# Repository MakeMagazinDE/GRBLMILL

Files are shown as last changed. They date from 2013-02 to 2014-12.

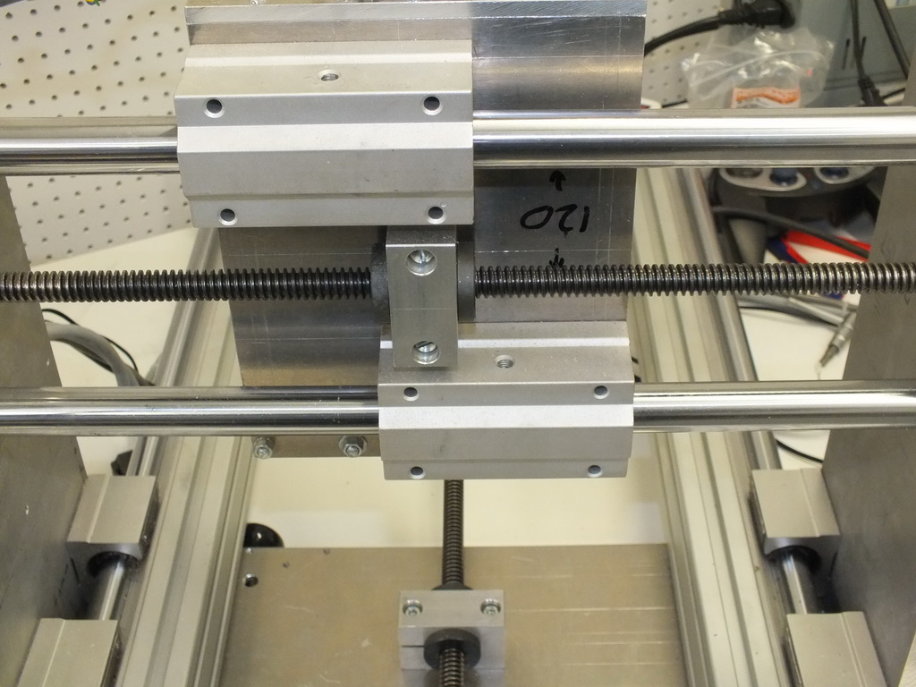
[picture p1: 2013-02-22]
BILDER/DSCF5111.JPG

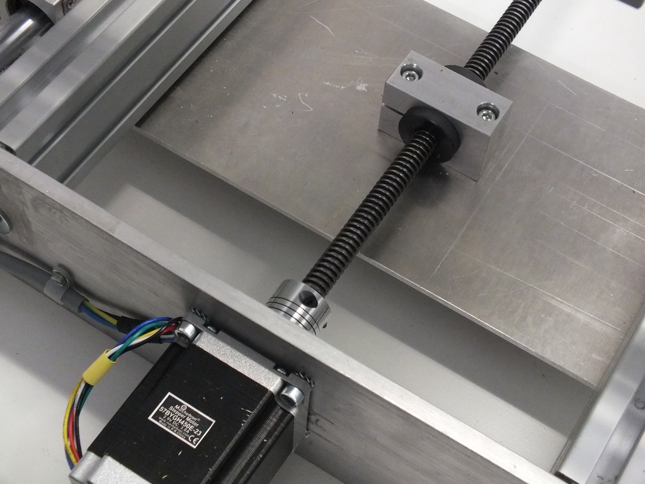
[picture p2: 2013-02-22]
BILDER/DSCF5087.JPG

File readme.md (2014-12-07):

GRBLMILL
========

3D-Positionierer/Fräse aus c't Hacks 01/2013

Verzeichnis GRBL: Firmware für Atmel ATmega328 mit Arduino-Bootloader, z.B. AT-Mini Board von mikroElektronika

- Mechanische Pläne für Selbstbau-Fräse
- Bezugsquellen
- Original-Unterlagen chin. Hersteller

Alle Angaben ohne Gewähr

Schaltbilder zu chinesischen TB6560-Schrittmotortreiberkarten 
und unsere GRBL-Schrittmotorsteuerung siehe auch Repo heise/TB6560-BOARDS

Obsoletes Projekt. Für neuere Aufbauten empfehlen wir unser Pojekt GRBL-Jogger (siehe Repository GRBL-JOG).

by Carsten Meyer, c't Hacks (cm@ct.de)

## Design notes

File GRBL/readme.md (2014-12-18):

Note: Obsolete project. Please use heise/GRBL-JOG instead.

h1. Grbl - An embedded g-code interpreter and motion-controller for the Arduino/AVR328 microcontroller
    
Grbl is a no-compromise, high performance, low cost alternative to parallel-port-based motion control for CNC milling. It will run on a vanilla Arduino (Duemillanove/Uno) as long as it sports an Atmega 328. 

The controller is written in highly optimized C utilizing every clever feature of the AVR-chips to achieve precise timing and asynchronous operation. It is able to maintain more than 30kHz of stable, jitter free control pulses.

It accepts standards-compliant G-code and has been tested with the output of several CAM tools with no problems. Arcs, circles and helical motion are fully supported, as well as, other basic functional g-code commands. Functions and variables are not currently supported, but may be included in future releases in a form of a pre-processor.

Grbl includes full acceleration management with look ahead. That means the controller will look up to 18 motions into the future and plan its velocities ahead to deliver smooth acceleration and jerk-free cornering.

*Changelog for v0.8a3 from v0.8 by cm@ct.de:*
  - Q&D Homing implemented on G28 or G30 command
  - M100 command for resetting external pulse counter
  - Defaults for c't Mill project on 3mm or 6mm threads
  - Spindle direction output deleted
  - Supports red "BUSY" LED on MINI-AT board from MikroE.com
  
*Changelog for v0.8 from v0.7:*
  - *ALPHA status: _Under heavy development. Code state may significantly change with each push as new features are integrated._*
  - Major structural overhaul to allow for multi-tasking events and new feature sets
  - New run-time command control: Feed hold (pause), Cycle start (resume), Reset (abort), Status reporting
  - Controlled feed hold with deceleration to ensure no skipped steps and loss of location.
  - After feed hold, cycle accelerations are re-planned and may be resumed.
  - Re-factored g-code parser with robust error-checking.
  - Work coordinate system (G54), offsets(G92), and machine coordinate system support. G10 work coordinate settings support. (Up to 6 work coordinate systems(G54-G59) available as a compile-time option.)
  - Program stop(M0,M1*,M2,M30) initial support. Optional stop to do.
  - System reset re-initializes grbl without resetting the Arduino and retains machine/home position and work coordinates.
  - Restructured planner and stepper modules to become independent and ready for future features.
  - Planned features: Jog mode, status reporting, runtime settings such as toggling block delete, XON/XOFF flow control.
  - Reduce serial read buffer to 128 characters and increased write buffer to 64 characters.
  - Misc bug fixes and removed deprecated acceleration enabled code.

*Important note for Atmega 168 users:* Going forward, support for Atmega 168 will be dropped due to its limited memory and speed. However, legacy Grbl v0.51 "in the branch called 'v0_51' is still available for use.

_The project was initially inspired by the Arduino GCode Interpreter by Mike Ellery_

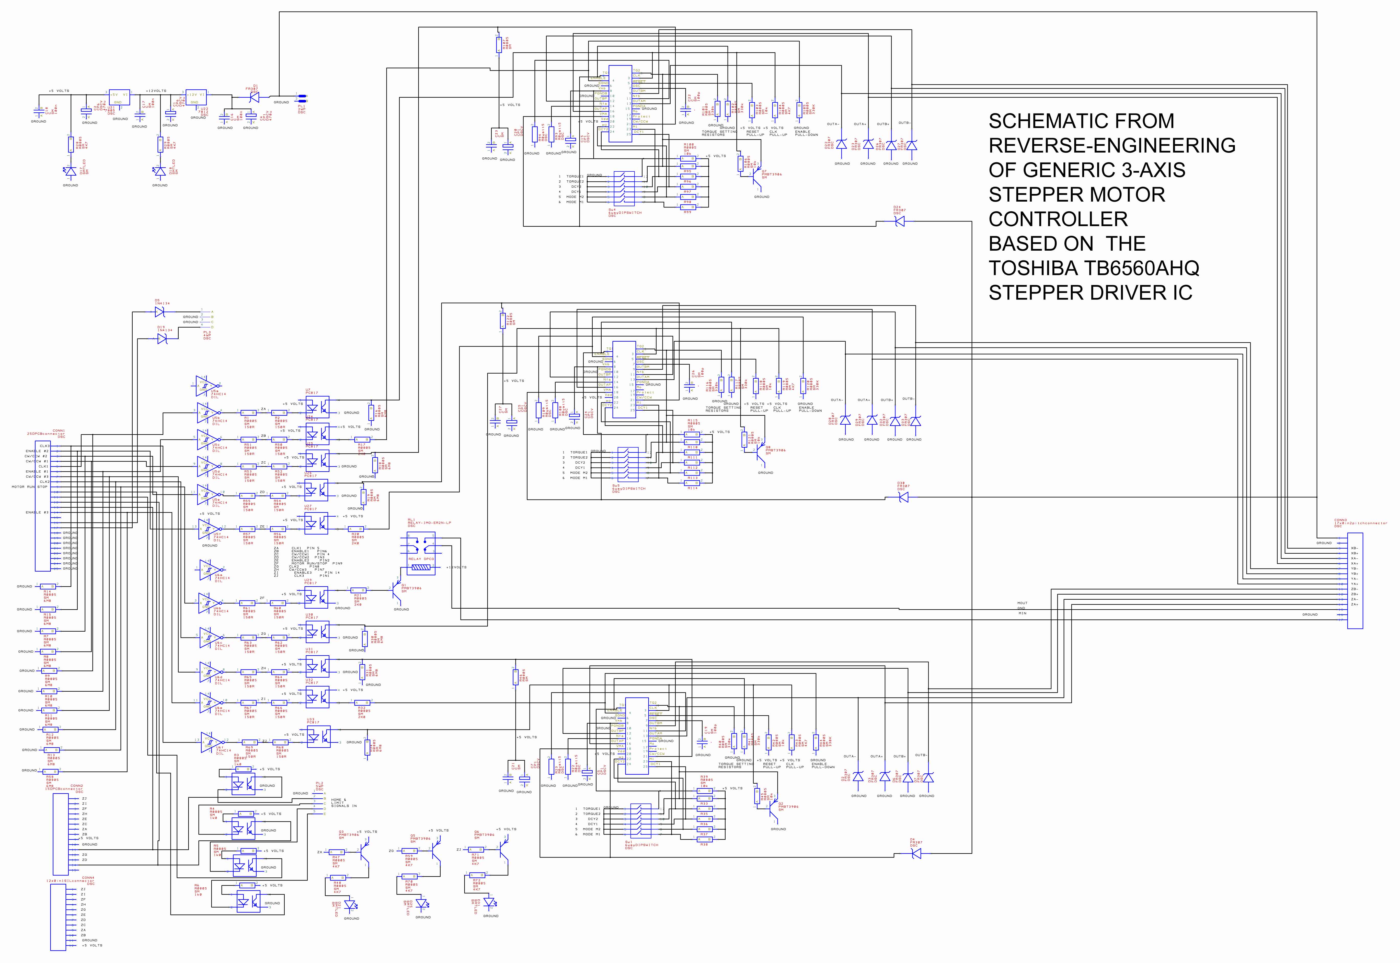
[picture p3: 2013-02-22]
GRBL/doc/REVERSESTEPPER.jpg

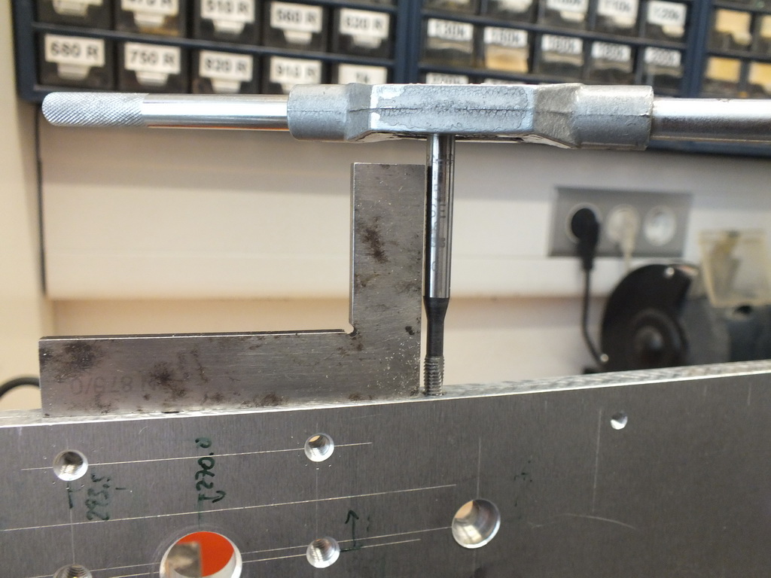
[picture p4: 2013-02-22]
BILDER/bild5.JPG

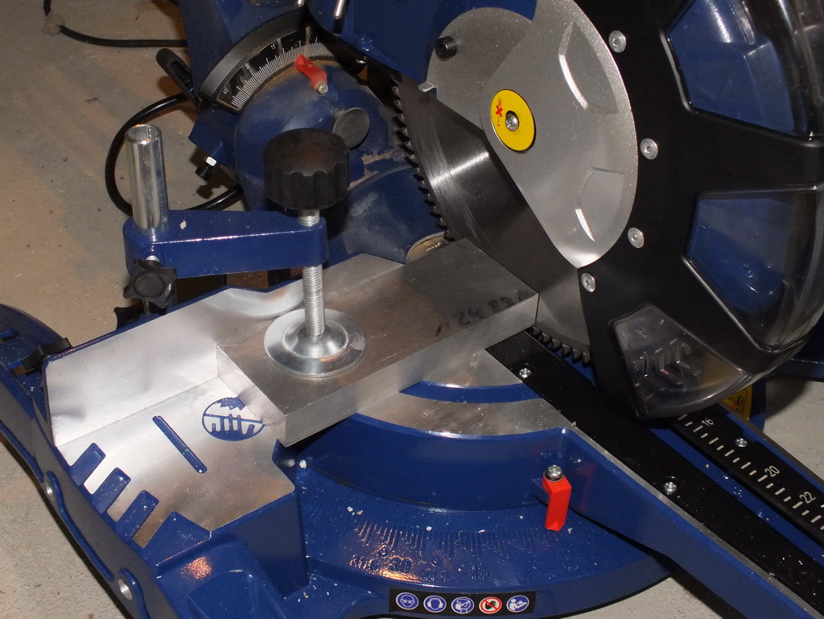
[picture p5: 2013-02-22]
BILDER/bild7.JPG

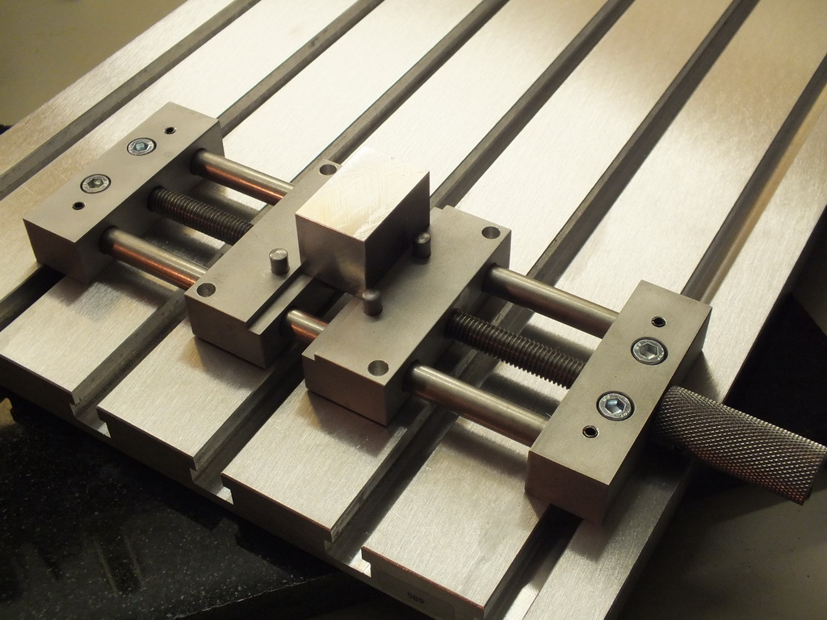
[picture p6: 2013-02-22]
BILDER/bild22.JPG

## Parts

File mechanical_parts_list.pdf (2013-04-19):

Stückliste c't-Portalfräse | Version 600 x 300 mm
Pos. | Bezeichnung | Abmessungen/Anmerkung | Stück | Einzelpreis Gesamtpreis Lieferant

X-Achse und Rahmen
1 | CNC Set 20 x 600 supported, "grün", 4 Wagen | 20 x 600 mm | 1 | 75,50 € | 75,50 € | http://stores.ebay.de/cnc-discount
2 | Hammermuttern | M5 Nut 8 | 20 | 0,28 € | 5,60 € | http://stores.ebay.de/aluprofiltechnik
3 | Alu-Profil Nut 8 | 60 x 30 Nut 8, 600 mm | 2 | 8,10 € | 16,20 € | http://stores.ebay.de/aluprofiltechnik
4 | Alu-Platte vorn/hinten | 80 x 420 x 8 mm Alu-Platte 2017 | 2 | 8,00 € | 16,00 € | http://www.metall-kunststoffhandel.de/shop/
| Y-Achse
5 | Y-Portal seitlich | 150 x 350 x 10 mm Alu-Platte 2017 | 2 | 11,87 € | 23,74 € | http://www.metall-kunststoffhandel.de/shop/
6 | Y-Traverse oben, Y-Traverse unten | 150 x 420 x 5 mm Alu-Blech 2017 | 2 | 16,44 € | 32,88 € | http://www.metall-kunststoffhandel.de/shop/
7 | Präzisionswelle | 20 x 400 mm | 2 | 8,80 € | 17,60 € | http://stores.ebay.de/Metallbau-Pietrzak
8 | Linearlager (ET)SCS20LUU | | 2 | 12,95 € | 25,90 € | http://stores.ebay.de/mayerundschulze-maschinen
9 | Linearlager (ET)SCS20UU | Alternative zu Pos. 8: 4x | 0 | 6,95 € | 0,00 € | http://stores.ebay.de/mayerundschulze-maschinen
10 | Wellenhalter Wandmontage (ET)SHF20 | falls Welle ohne Gewinde | 4 | 4,90 € | 19,60 € | http://stores.ebay.de/mayerundschulze-maschinen
| Z-Achse
11 | Präzisionswelle | 16 x 200 mm | 2 | 4,00 € | 8,00 € | http://stores.ebay.de/Metallbau-Pietrzak
12 | Linearlager (ET)SCS16LUU | | 2 | 11,25 € | 22,50 € | http://stores.ebay.de/mayerundschulze-maschinen
13 | Wellenhalter (ET)SK16 stehend | | 2 | 3,50 € | 7,00 € | http://stores.ebay.de/mayerundschulze-maschinen
14 | CNC Linearführung 16x 200mm Set "Blau" | Alternative zu Pos. 11 bis 13: 1x | 0 | 51,60 € | 0,00 € | http://stores.ebay.de/cnc-discount
15 | Wellenhalter Wandmontage (ET)SHF16 | | 2 | 3,50 € | 7,00 € | http://stores.ebay.de/mayerundschulze-maschinen
16 | Z-Träger Grundplatte | 200 x 155 x 8 mm Alu-Platte 2017 | 1 | 7,02 € | 7,02 € | http://www.metall-kunststoffhandel.de/shop/
17 | Spindelmotor-Träger | 130 x 155 x 8 mm Alu-Platte 2017 | 1 | 6,62 € | 6,62 € | http://www.metall-kunststoffhandel.de/shop/
18 | Schrittmotorträger oben | 65 x 155 x 6 mm Alu-Platte 2017 | 1 | 5,10 € | 5,10 € | http://www.metall-kunststoffhandel.de/shop/
| Sonstiges
19 | Nylatron-Muttern | TR12x3 mit Rändel, halb | 6 | 3,95 € | 23,70 € | http://www.cnc-laden.de
20 | Mutterblock zum Klemmen | 54 x 35 x 24 mm, TR12 | 3 | 14,60 € | 43,80 € | http://www.cnc-laden.de
21 | Trapezspindel | TR12x3, 1000 mm | 2 | 6,70 € | 13,40 € | http://stores.ebay.de/Metallbau-Pietrzak
22 | Wellenkupplung 6,35/12 flexibel | China: ca. 4 € | 2 | 8,00 € | 16,00 € | http://stores.ebay.de/dold-mechatronik
23 | Wellenkupplung 6,35/12 starr | für Z-Achse, ggf. aufbohren auf 12 mm 1 | 6,00 € | 6,00 € | http://stores.ebay.de/dold-mechatronik
24 | Flanschlager Mini 12 mm, KFL001 | | 4 | 6,78 € | 27,12 € | http://www.kugellager-express.de
25 | Spannhals-Befestigung 43mm | Aufnahme etwas zu groß (44mm)! | 1 | 24,30 € | 24,30 € | http://www.cnc-laden.de
26 | Hammermuttern | M6 Nut 8 | 10 | 0,28 € | 2,80 € | http://stores.ebay.de/aluprofiltechnik
| Gesamt | | | | 453,38 €
Z-Achse Alternative | schmaler, auch zum Betrieb mit Gravuranschlag, 50 mm Verfahrweg
Linearlager mit quadratischem Flansch 16mm LMEK16UU | 2 | 7,20 € | http://stores.ebay.de/dold-mechatronik
| Linearlager 16mm SCE16SUU | | 4 | 7,90 € | | http://stores.ebay.de/dold-mechatronik
| CNC Linearführung 16x 250mm Set "Blau" | | 1 | 54,00 € | 54,00 € | http://stores.ebay.de/cnc-discount
| Z-Träger Grundplatte | 200 x 135 x 8 mm Alu-Platte 2017 | 1 | 7,02 € | 7,02 € | http://www.metall-kunststoffhandel.de/shop/
| Spindelmotor-Träger | 130 x 135 x 8 mm Alu-Platte 2017 | 1 | 6,62 € | 6,62 € | http://www.metall-kunststoffhandel.de/shop/
| Schrittmotorträger oben | 65 x 135 x 6 mm Alu-Platte 2017 | 1 | 5,10 € | 5,10 € | http://www.metall-kunststoffhandel.de/shop/
| Zubehör
27 | Spannhals-Adapter 43 mm auf Ferm oder Drehmel | | 0 | 23,00 € | 0,00 € | http://www.cnc-laden.de
28 | Fräsmotor Kress FME-1051 | | 0 | 173,00 € | 0,00 € | http://www.amazon.de
29 | Fräsmotor Noname | Alternative zu Pos. 28 | 1 | 54,00 € | 54,00 € | http://myworld.ebay.de/jancocaucau3/
30 | T-Nutenplatte 4030 | 400 x 300 mm | 0 | 129,00 € | 0,00 € | http://www.maschinen-werkzeuge.com
31 | Vakuumtische | diverse | 0 | | 0,00 € | http://www.vakuumtisch.de/
32 | Spannpratzen-Satz M6 | | 0 | 64,00 € | 0,00 € | http://stores.ebay.de/CNC-Maschinen-Shop
33 | Schrittmotor NEMA23 1 Nm, 2 A | 57x 57 mm Flansch | 0 | 29,90 € | 0,00 € | http://www.frasa-cnc.de
34 | Schrittmotor NEMA23 1,85 Nm, 2 A | Alternative zu Pos. 32 | 0 | 37,90 € | 0,00 € | http://stores.ebay.de/CNCShop-at
35 | Schrittmotorsteuerung TB6560 | | 0 | 29,90 € | 0,00 € | diverse ebay-Anbieter
36 | Schrittmotorsteuerung TB6560 | Alternative zu Pos. 34 | 0 | 32,89 € | 0,00 € | http://stores.ebay.de/1-netshop-best
37 | Not-Aus-Schalter Aufputz | | 1 | 12,95 € | 12,95 € | http://stores.ebay.de/klinger-und-born
| Alternativprodukte (ggf. Änderung nötig)
| Trapezspindeln TR12 x 6 mit Muttern | Alternative zu TR12x3, 1000 mm | 2 | | | http://stores.ebay.de/dold-mechatronik
| (doppelte Steigung wie TR12x3, schnellerer Eilgang)
| Flanschlager für X-Achse, UCF201 (größer) | | 1 | 4,40 € | 4,40 € | http://stores.ebay.de/Panta-Shop
| Kugelumlauf-Führungen, Kugelumlauf-Spindeln | diverse | | | | http://stores.ebay.de/Linear-Motion-Products

## Technische Daten

| Verfahrweg | 450 x 245 mm | | | | Alle Angaben ohne Gewähr.
| Durchlasshöhe | 85 mm | | | | Stand 19.04.2013
| Verfahrgeschwindigkeit, Eilgang | 1500 mm/min (2800 bei 6mm Trapezsp.) | | | | Statt Alu 2017 auch Qualität 2007 verwendbar.
| Stromversorgung | 24V/5A | | | | Autor: Carsten Meyer, Redaktion c't Hacks, cm@ct.d

Artikel-Link

http://www.ebay.de/itm/CNC-Set-20-x-600mm-Linearfuhrung-Linear-Guide-Rail-Stage-Frase-Welle-/221043413143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

http://www.ebay.de/itm/Profil-30-x-60-Nut-8-Aluprofil-Profil-Aluminium-Alu-/150655377758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

http://www.metall-kunststoffhandel.de/shop/2007-flachstange-p-147.html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

http://www.ebay.de/itm/Prazisionswelle-16-mm-100-990mm-wahlbar-20-m-Tol-h6-geschliffen-cf53-1511-/390416782056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

http://cnc-laden.de/cnc-shop/Trapezgewindemuttern-12x3/Trapezgewindemutter-12x3-Nylatron-Raendel.htmlhttp://cnc-laden.de/cnc-shop/Mutterbloecke/Mutterblock-Trapezgew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

http://www.kugellager-express.de/Gehaeuselager/Miniatur-Flanschlager-KFL---/Miniatur-Flanschlager-KFL001---Welle--12-mm--SILBER-Serie-.htmlhttp://cnc-laden.de/cnc-sh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

http://www.ebay.de/itm/CNC-Linearfuhrung-16x-200mm-Set-Blau-2x-lange-Linearwagen-Wellen-Wellenhalter-/221171302185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

http://cnc-laden.de/cnc-shop/Spannhals-Adapter.html
http://www.amazon.de/Kress-1050-FME-Watt-Fr%C3%A4smotor/dp/B004U5F4H0

http://www.maschinen-werkzeuge.com/tnutenplatte-4030-p-1372.html

http://www.ebay.de/itm/58-Teiliger-Spannpratzen-Satz-M6-8er-Nut-/260923137767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

e

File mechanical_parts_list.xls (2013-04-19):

Stückliste c't-Portalfräse |  | Version 600 x 300 mm
Pos. | Bezeichnung | Abmessungen/Anmerkung | Stück | Einzelpreis | Gesamtpreis | Lieferant | Artikel-Link
 | X-Achse und Rahmen
1 | CNC Set 20 x 600 supported, "grün", 4 Wagen | 20 x 600 mm | 1 | 75.50 € | 75.50 € | http://stores.ebay.de/cnc-discount | http://www.ebay.de/itm/CNC-Set-20-x-600mm-Linearfuhrung-Linear-Guide-Rail-Stage-Frase-Welle-/221043413143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
2 | Hammermuttern | M5 Nut 8 | 20 | 0.28 € | 5.60 € | http://stores.ebay.de/aluprofiltechnik
3 | Alu-Profil Nut 8 | 60 x 30 Nut 8, 600 mm | 2 | 8.10 € | 16.20 € | http://stores.ebay.de/aluprofiltechnik | http://www.ebay.de/itm/Profil-30-x-60-Nut-8-Aluprofil-Profil-Aluminium-Alu-/150655377758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
4 | Alu-Platte vorn/hinten | 80 x 420 x 8 mm Alu-Platte 2017 | 2 | 8.00 € | 16.00 € | http://www.metall-kunststoffhandel.de/shop/
 | Y-Achse
5 | Y-Portal seitlich | 150 x 350 x 10 mm Alu-Platte 2017 | 2 | 11.87 € | 23.74 € | http://www.metall-kunststoffhandel.de/shop/ | http://www.metall-kunststoffhandel.de/shop/2007-flachstange-p-147.html?osCsid=4d8f5ec64735d1192282b06c5dd4326e
6 | Y-Traverse oben, Y-Traverse unten | 150 x 420 x 5 mm Alu-Blech 2017 | 2 | 16.44 € | 32.88 € | http://www.metall-kunststoffhandel.de/shop/ | http://www.metall-kunststoffhandel.de/shop/aluminium-platte-0050-12017-p-2146_150_420.html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
7 | Präzisionswelle | 20 x 400 mm | 2 | 8.80 € | 17.60 € | http://stores.ebay.de/Metallbau-Pietrzak | http://www.ebay.de/itm/Prazisionswelle-20-mm-100-990mm-wahlbar-22-m-Tol-h6-geschliffen-cf53-1513-/390416782226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
8 | Linearlager (ET)SCS20LUU |  | 2 | 12.95 € | 25.90 € | http://stores.ebay.de/mayerundschulze-maschinen | http://www.ebay.de/itm/Linearlager-Linearwagen-Linearschlitten-SCS20LUU-20-mm-Welle-ETSCS20LUU-/150836635461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
9 | Linearlager (ET)SCS20UU | Alternative zu Pos. 8: 4x | 0 | 6.95 € | 0.00 € | http://stores.ebay.de/mayerundschulze-maschinen | http://www.ebay.de/itm/Linearlager-Linearwagen-Linearschlitten-SCS20UU-20-mm-Welle-ETSCS20UU-/150836635489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
10 | Wellenhalter Wandmontage (ET)SHF20 | falls Welle ohne Gewinde | 4 | 4.90 € | 19.60 € | http://stores.ebay.de/mayerundschulze-maschinen | http://www.ebay.de/itm/Wellenhalter-Wandmontage-Stahlwelle-20-mm-ETSHF20-/150908306739?pt=LH_DefaultDomain_77
 | Z-Achse
11 | Präzisionswelle | 16 x 200 mm | 2 | 4.00 € | 8.00 € | http://stores.ebay.de/Metallbau-Pietrzak | http://www.ebay.de/itm/Prazisionswelle-16-mm-100-990mm-wahlbar-20-m-Tol-h6-geschliffen-cf53-1511-/390416782056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
12 | Linearlager (ET)SCS16LUU |  | 2 | 11.25 € | 22.50 € | http://stores.ebay.de/mayerundschulze-maschinen | http://www.ebay.de/itm/Linearlager-Linearwagen-Linearschlitten-SCS16LUU-16-mm-Welle-ETSCS16LUU-/150836085462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
13 | Wellenhalter (ET)SK16 stehend |  | 2 | 3.50 € | 7.00 € | http://stores.ebay.de/mayerundschulze-maschinen | http://www.ebay.de/itm/Wellenhalter-stehend-Bodenmontage-Stahlwelle-16-mm-ETSK16-/150789522903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
14 | CNC Linearführung 16x 200mm Set "Blau" | Alternative zu Pos. 11 bis 13: 1x | 0 | 51.60 € | 0.00 € | http://stores.ebay.de/cnc-discount | http://www.ebay.de/itm/CNC-Linearfuhrung-16x-200mm-Set-Blau-2x-lange-Linearwagen-Wellen-Wellenhalter-/221171302185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
15 | Wellenhalter Wandmontage (ET)SHF16 |  | 2 | 3.50 € | 7.00 € | http://stores.ebay.de/mayerundschulze-maschinen | http://www.ebay.de/itm/Wellenhalter-Wandmontage-Stahlwelle-16-mm-ETSHF16-/150838904770?pt=LH_DefaultDomain_77
16 | Z-Träger Grundplatte | 200 x 155 x 8 mm Alu-Platte 2017 | 1 | 7.02 € | 7.02 € | http://www.metall-kunststoffhandel.de/shop/ | http://www.metall-kunststoffhandel.de/shop/2007-flachstange-p-131_200_0.html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
17 | Spindelmotor-Träger | 130 x 155 x 8 mm Alu-Platte 2017 | 1 | 6.62 € | 6.62 € | http://www.metall-kunststoffhandel.de/shop/ | http://www.metall-kunststoffhandel.de/shop/2007-flachstange-p-131_200_0.html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
18 | Schrittmotorträger oben | 65 x 155 x 6 mm Alu-Platte 2017 | 1 | 5.10 € | 5.10 € | http://www.metall-kunststoffhandel.de/shop/ | http://www.metall-kunststoffhandel.de/shop/2007-flachstange-p-131_200_0.html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
 | Sonstiges
19 | Nylatron-Muttern | TR12x3 mit Rändel, halb | 6 | 3.95 € | 23.70 € | http://www.cnc-laden.de | http://cnc-laden.de/cnc-shop/Trapezgewindemuttern-12x3/Trapezgewindemutter-12x3-Nylatron-Raendel.html
20 | Mutterblock zum Klemmen | 54 x 35 x 24 mm, TR12 | 3 | 14.60 € | 43.80 € | http://www.cnc-laden.de | http://cnc-laden.de/cnc-shop/Mutterbloecke/Mutterblock-Trapezgewindemutter-12x3-Klemmen.html
21 | Trapezspindel | TR12x3, 1000 mm | 2 | 6.70 € | 13.40 € | http://stores.ebay.de/Metallbau-Pietrzak | http://www.ebay.de/itm/Trapezgewindespindel-TR12x3-rechts-DIN103-150mm-3508-/220385890978?pt=Motoren_Getriebe
22 | Wellenkupplung 6,35/12 flexibel | China: ca. 4 € | 2 | 8.00 € | 16.00 € | http://stores.ebay.de/dold-mechatronik | http://www.ebay.de/itm/Wellenkupplung-Kupplung-RB-flexibel-D25L30-6-35-12-00mm-CNC-Schrittmotor-/270934044860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
23 | Wellenkupplung 6,35/12 starr | für Z-Achse, ggf. aufbohren auf 12 mm | 1 | 6.00 € | 6.00 € | http://stores.ebay.de/dold-mechatronik
24 | Flanschlager Mini 12 mm, KFL001 |  | 4 | 6.78 € | 27.12 € | http://www.kugellager-express.de | http://www.kugellager-express.de/Gehaeuselager/Miniatur-Flanschlager-KFL---/Miniatur-Flanschlager-KFL001---Welle--12-mm--SILBER-Serie-.html
25 | Spannhals-Befestigung 43mm | Aufnahme etwas zu groß (44mm)! | 1 | 24.30 € | 24.30 € | http://www.cnc-laden.de | http://cnc-laden.de/cnc-shop/Spannhals/Spannhals-Maschinenhalter-43-mm.html
26 | Hammermuttern | M6 Nut 8 | 10 | 0.28 € | 2.80 € | http://stores.ebay.de/aluprofiltechnik
 | Gesamt |  |  |  | 453.38 €
 | Z-Achse Alternative | schmaler, auch zum Betrieb mit Gravuranschlag, 50 mm Verfahrweg
 | Linearlager mit quadratischem Flansch 16mm LMEK16UU |  | 2 | 7.20 € |  | http://stores.ebay.de/dold-mechatronik
 | Linearlager 16mm SCE16SUU |  | 4 | 7.90 € |  | http://stores.ebay.de/dold-mechatronik
 | CNC Linearführung 16x 250mm Set "Blau" |  | 1 | 54.00 € | 54.00 € | http://stores.ebay.de/cnc-discount | http://www.ebay.de/itm/CNC-Linearfuhrung-16x-200mm-Set-Blau-2x-lange-Linearwagen-Wellen-Wellenhalter-/221171302185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
 | Z-Träger Grundplatte | 200 x 135 x 8 mm Alu-Platte 2017 | 1 | 7.02 € | 7.02 € | http://www.metall-kunststoffhandel.de/shop/ | http://www.metall-kunststoffhandel.de/shop/2007-flachstange-p-131_200_0.html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
 | Spindelmotor-Träger | 130 x 135 x 8 mm Alu-Platte 2017 | 1 | 6.62 € | 6.62 € | http://www.metall-kunststoffhandel.de/shop/ | http://www.metall-kunststoffhandel.de/shop/2007-flachstange-p-131_200_0.html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
 | Schrittmotorträger oben | 65 x 135 x 6 mm Alu-Platte 2017 | 1 | 5.10 € | 5.10 € | http://www.metall-kunststoffhandel.de/shop/ | http://www.metall-kunststoffhandel.de/shop/2007-flachstange-p-131_200_0.html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
 | Zubehör
27 | Spannhals-Adapter 43 mm auf Ferm oder Drehmel |  | 0 | 23.00 € | 0.00 € | http://www.cnc-laden.de | http://cnc-laden.de/cnc-shop/Spannhals-Adapter.html
28 | Fräsmotor Kress FME-1051 |  | 0 | 173.00 € | 0.00 € | http://www.amazon.de | http://www.amazon.de/Kress-1050-FME-Watt-Fr%C3%A4smotor/dp/B004U5F4H0
29 | Fräsmotor Noname | Alternative zu Pos. 28 | 1 | 54.00 € | 54.00 € | http://myworld.ebay.de/jancocaucau3/
30 | T-Nutenplatte 4030 | 400 x 300 mm | 0 | 129.00 € | 0.00 € | http://www.maschinen-werkzeuge.com | http://www.maschinen-werkzeuge.com/tnutenplatte-4030-p-1372.html
31 | Vakuumtische | diverse | 0 |  | 0.00 € | http://www.vakuumtisch.de/
32 | Spannpratzen-Satz M6 |  | 0 | 64.00 € | 0.00 € | http://stores.ebay.de/CNC-Maschinen-Shop | http://www.ebay.de/itm/58-Teiliger-Spannpratzen-Satz-M6-8er-Nut-/260923137767?pt=Gartenbauwerkzeuge
33 | Schrittmotor NEMA23 1 Nm, 2 A | 57x 57 mm Flansch | 0 | 29.90 € | 0.00 € | http://www.frasa-cnc.de | http://www.frasa-cnc.de/Dateien/product_info.php
34 | Schrittmotor NEMA23 1,85 Nm, 2 A | Alternative zu Pos. 32 | 0 | 37.90 € | 0.00 € | http://stores.ebay.de/CNCShop-at | http://www.ebay.de/itm/Schrittmotor-CNC-1-85-NM-1-8-2-0-A-neu-Frase-/400309646161?pt=Motoren_Getriebe
35 | Schrittmotorsteuerung TB6560 |  | 0 | 29.90 € | 0.00 € | diverse ebay-Anbieter | http://www.ebay.de/itm/High-quality-CNC-TB6560-3-Axis-Stepper-Motor-Driver-Controller-Board-with-fan-/261137574690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
36 | Schrittmotorsteuerung TB6560 | Alternative zu Pos. 34 | 0 | 32.89 € | 0.00 € | http://stores.ebay.de/1-netshop-best | http://www.ebay.de/itm/TB6560-3-Achsen-Schrittmotor-Steuerung-0-8-3-5A-Digital-/190705438039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
37 | Not-Aus-Schalter Aufputz |  | 1 | 12.95 € | 12.95 € | http://stores.ebay.de/klinger-und-born | http://www.ebay.de/itm/Schneider-Not-Aus-Taster-in-Gehause-/170958977700?pt=Elektromechanische_Bauelemente
 | Alternativprodukte (ggf. Änderung nötig)
 | Trapezspindeln TR12 x 6 mit Muttern | Alternative zu TR12x3, 1000 mm | 2 |  |  | http://stores.ebay.de/dold-mechatronik
 | (doppelte Steigung wie TR12x3, schnellerer Eilgang)
 | Flanschlager für X-Achse, UCF201 (größer) |  | 1 | 4.40 € | 4.40 € | http://stores.ebay.de/Panta-Shop
 | Kugelumlauf-Führungen, Kugelumlauf-Spindeln | diverse |  |  |  | http://stores.ebay.de/Linear-Motion-Products
Technische Daten
 | Verfahrweg | 450 x 245 mm |  |  |  | Alle Angaben ohne Gewähr.
 | Durchlasshöhe | 85 mm |  |  |  | Stand 19.04.2013
 | Verfahrgeschwindigkeit, Eilgang | 1500 mm/min (2800 bei 6mm Trapezsp.) |  |  |  | Statt Alu 2017 auch Qualität 2007 verwendbar.
 | Stromversorgung | 24V/5A |  |  |  | Autor: Carsten Meyer, Redaktion c't Hacks, cm@ct.de

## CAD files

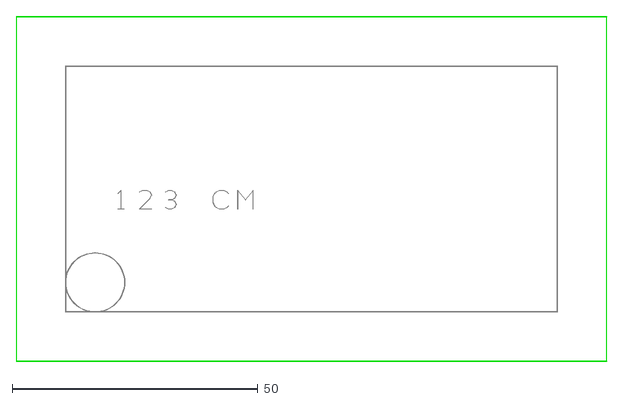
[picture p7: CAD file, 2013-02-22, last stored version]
LABVIEW/DRILLDATA/test_hpgl.dxf
120.2 x 70.2

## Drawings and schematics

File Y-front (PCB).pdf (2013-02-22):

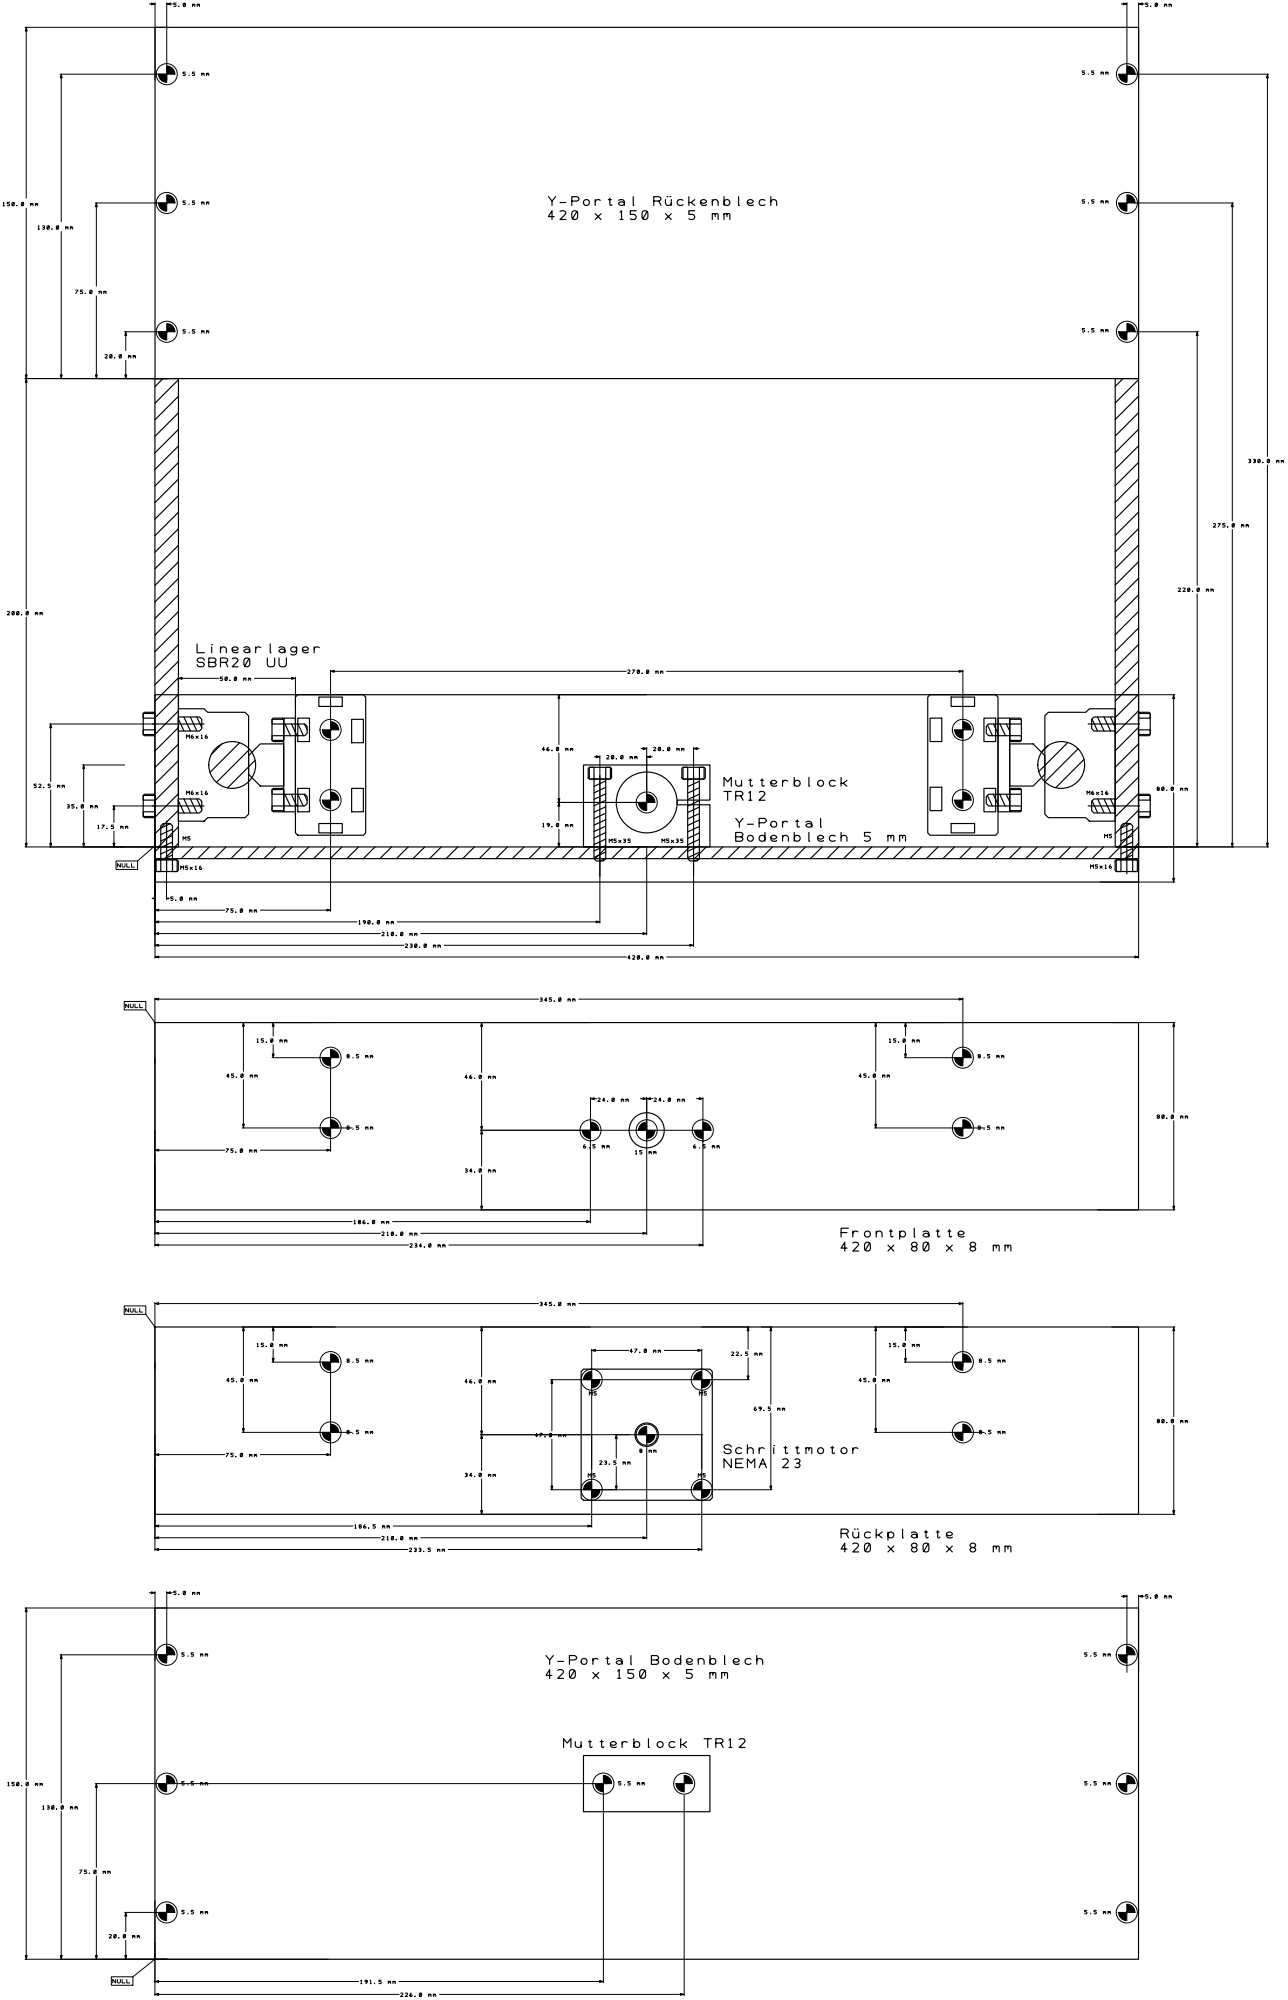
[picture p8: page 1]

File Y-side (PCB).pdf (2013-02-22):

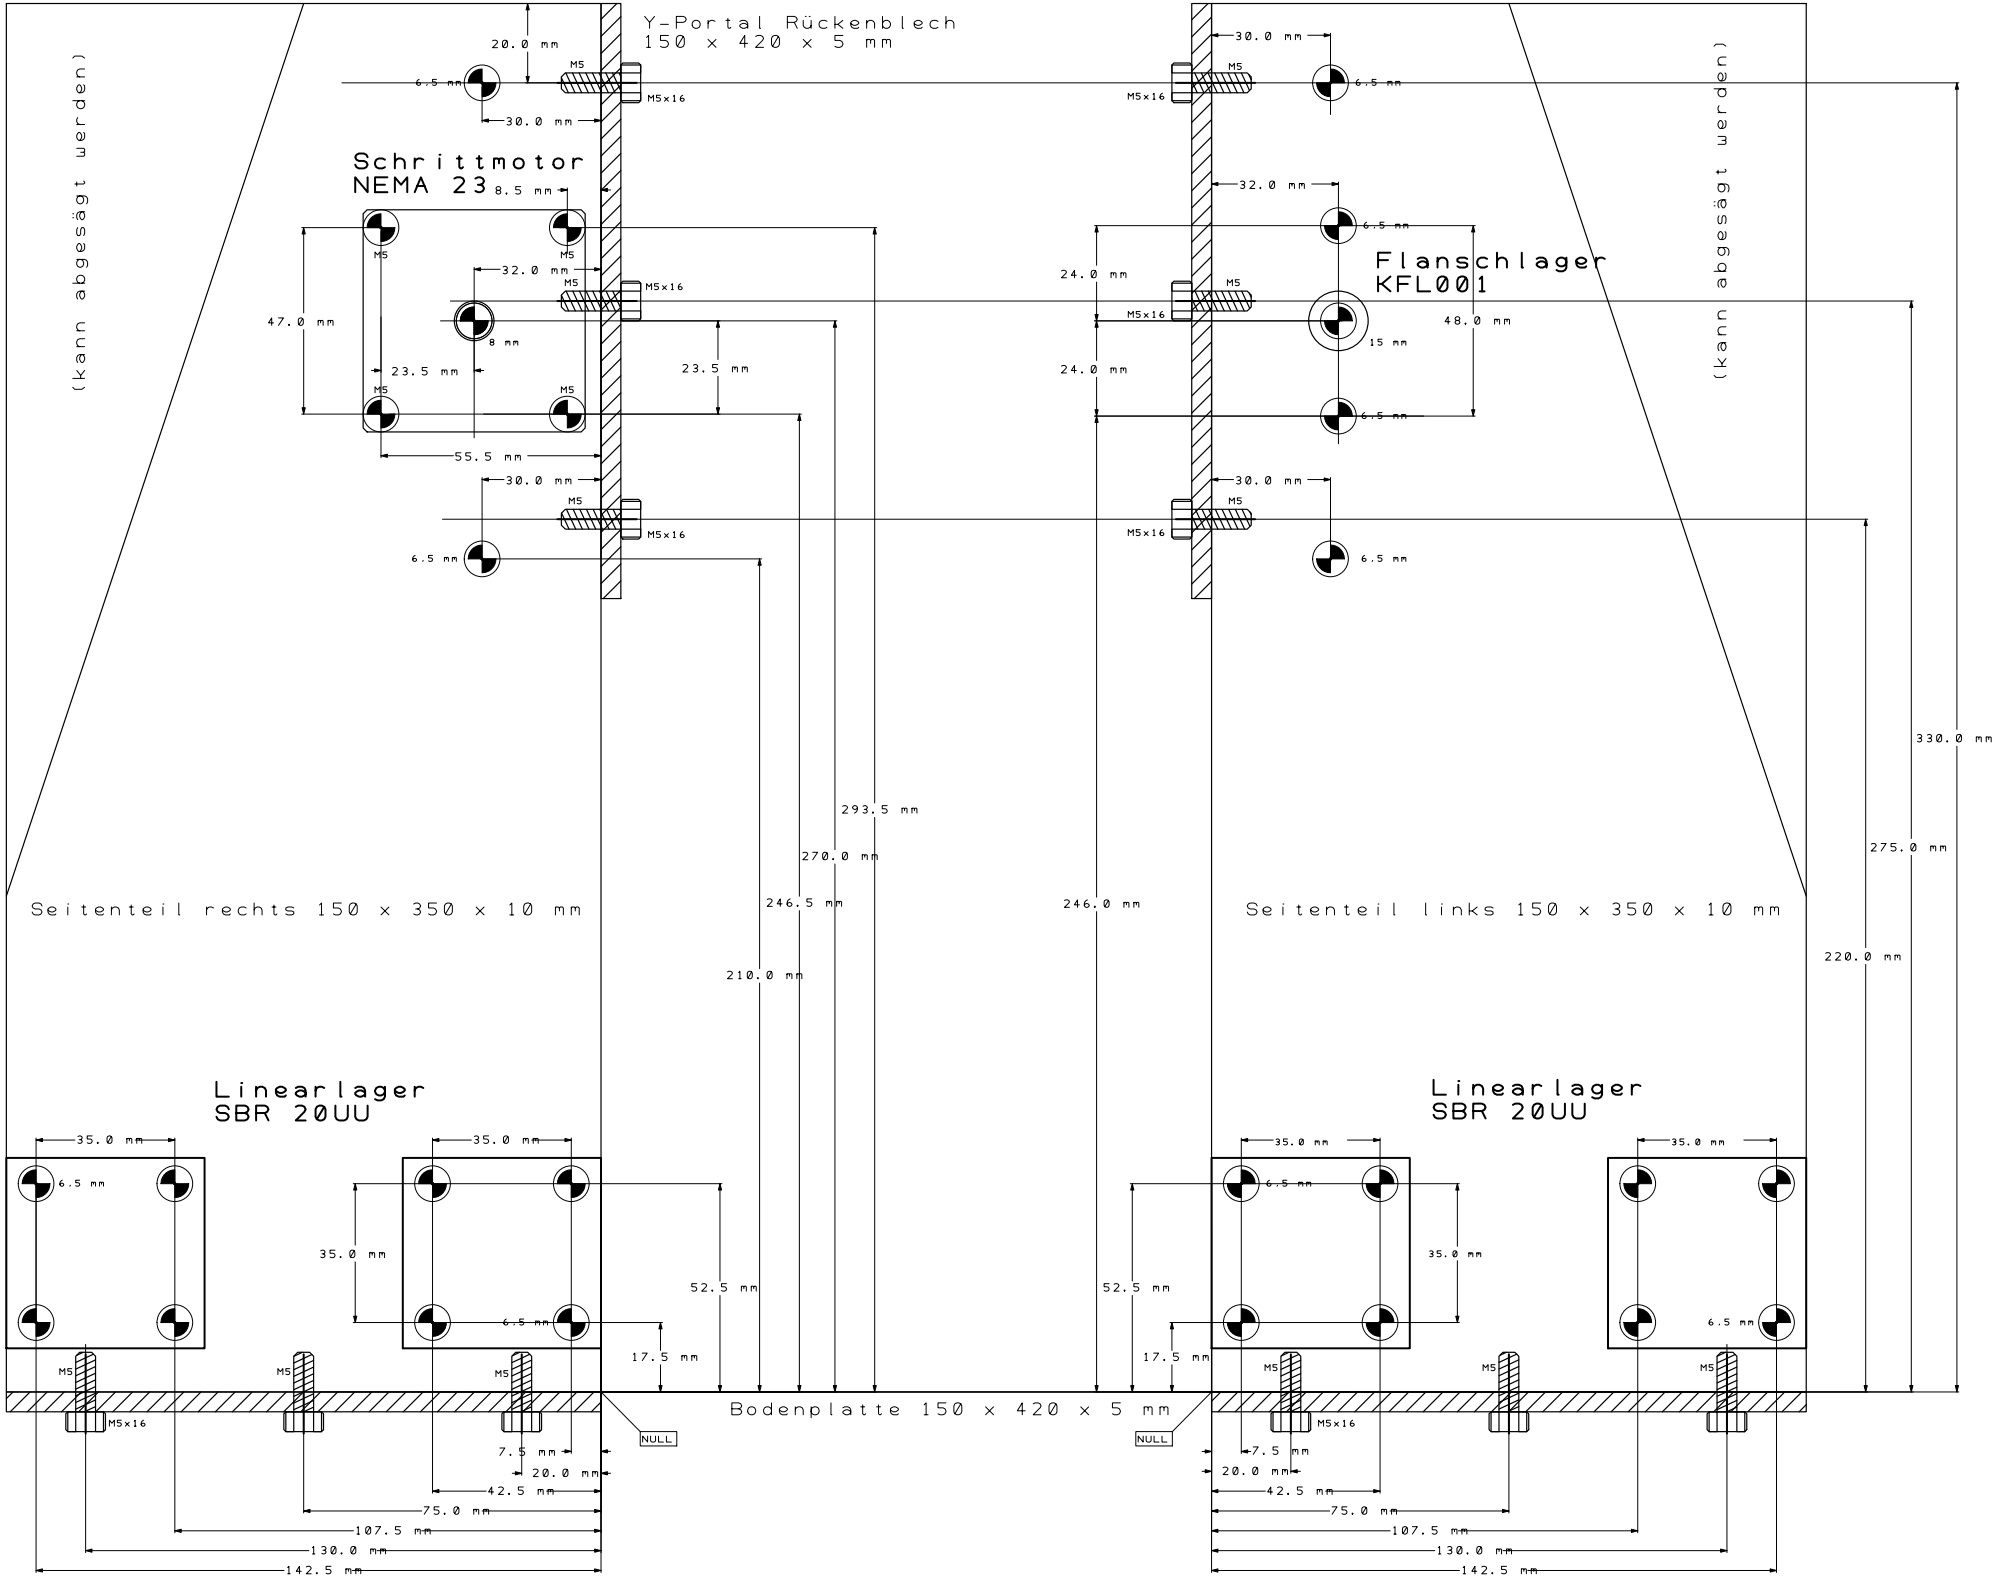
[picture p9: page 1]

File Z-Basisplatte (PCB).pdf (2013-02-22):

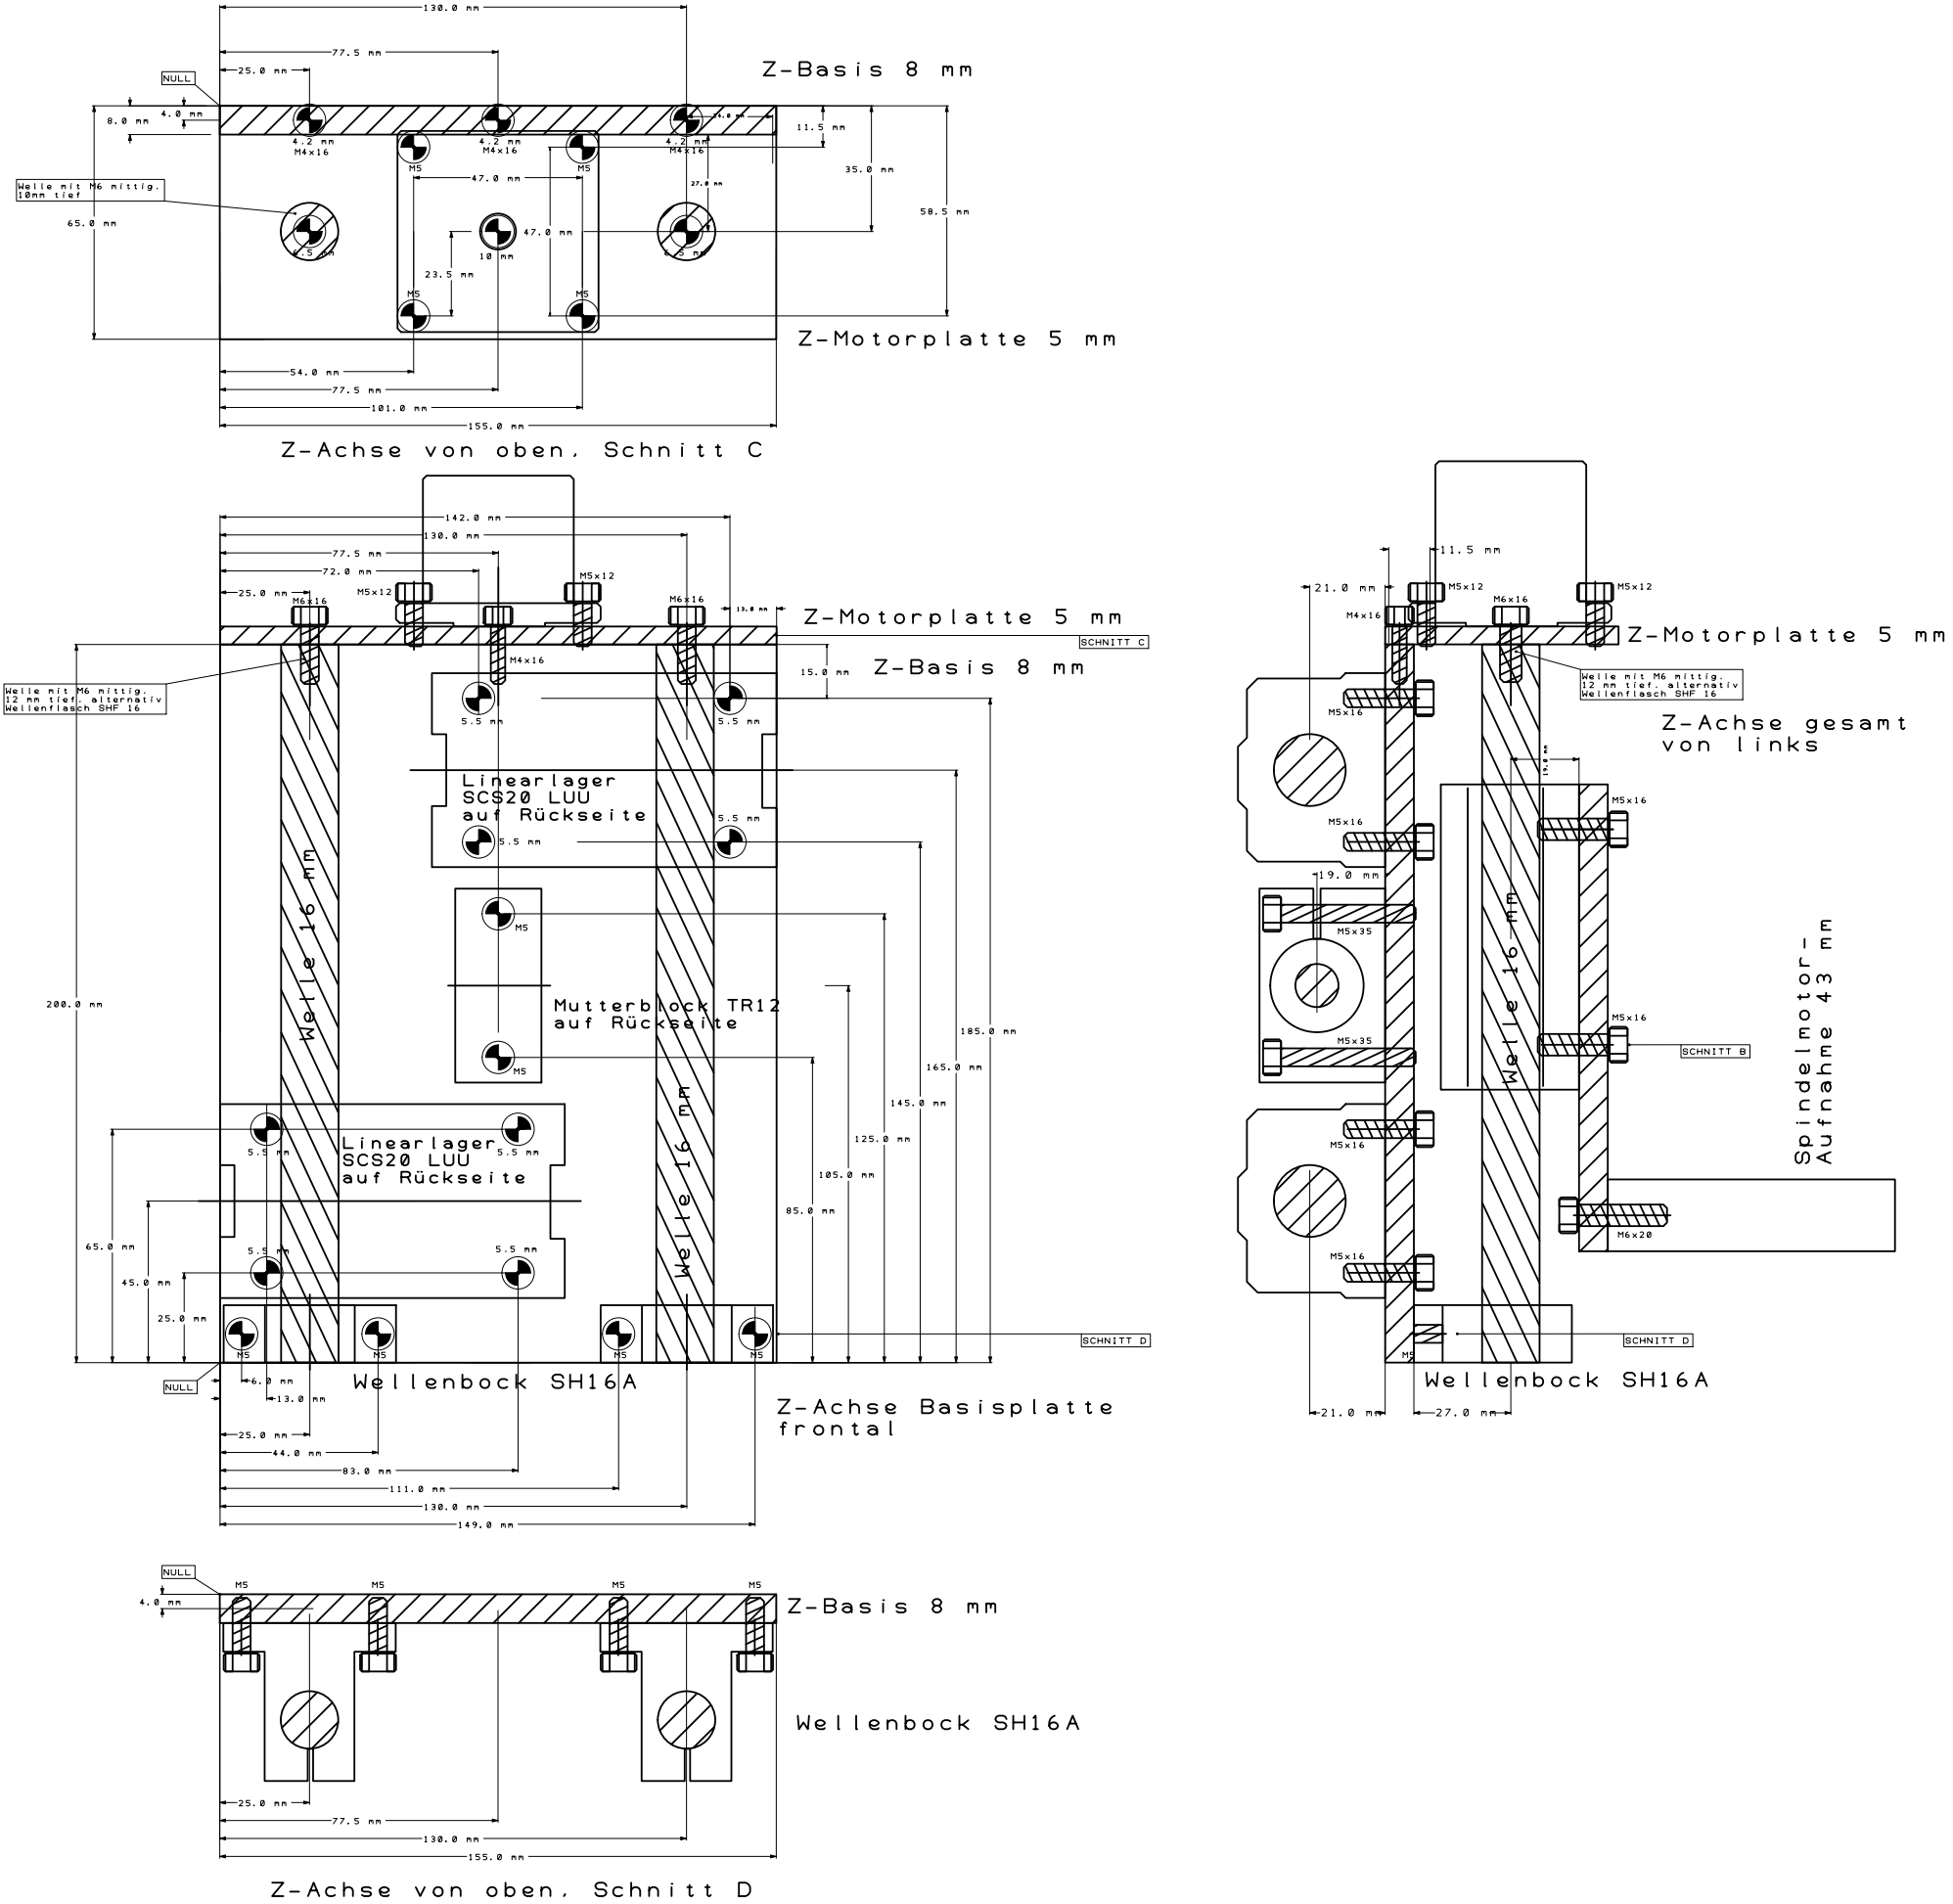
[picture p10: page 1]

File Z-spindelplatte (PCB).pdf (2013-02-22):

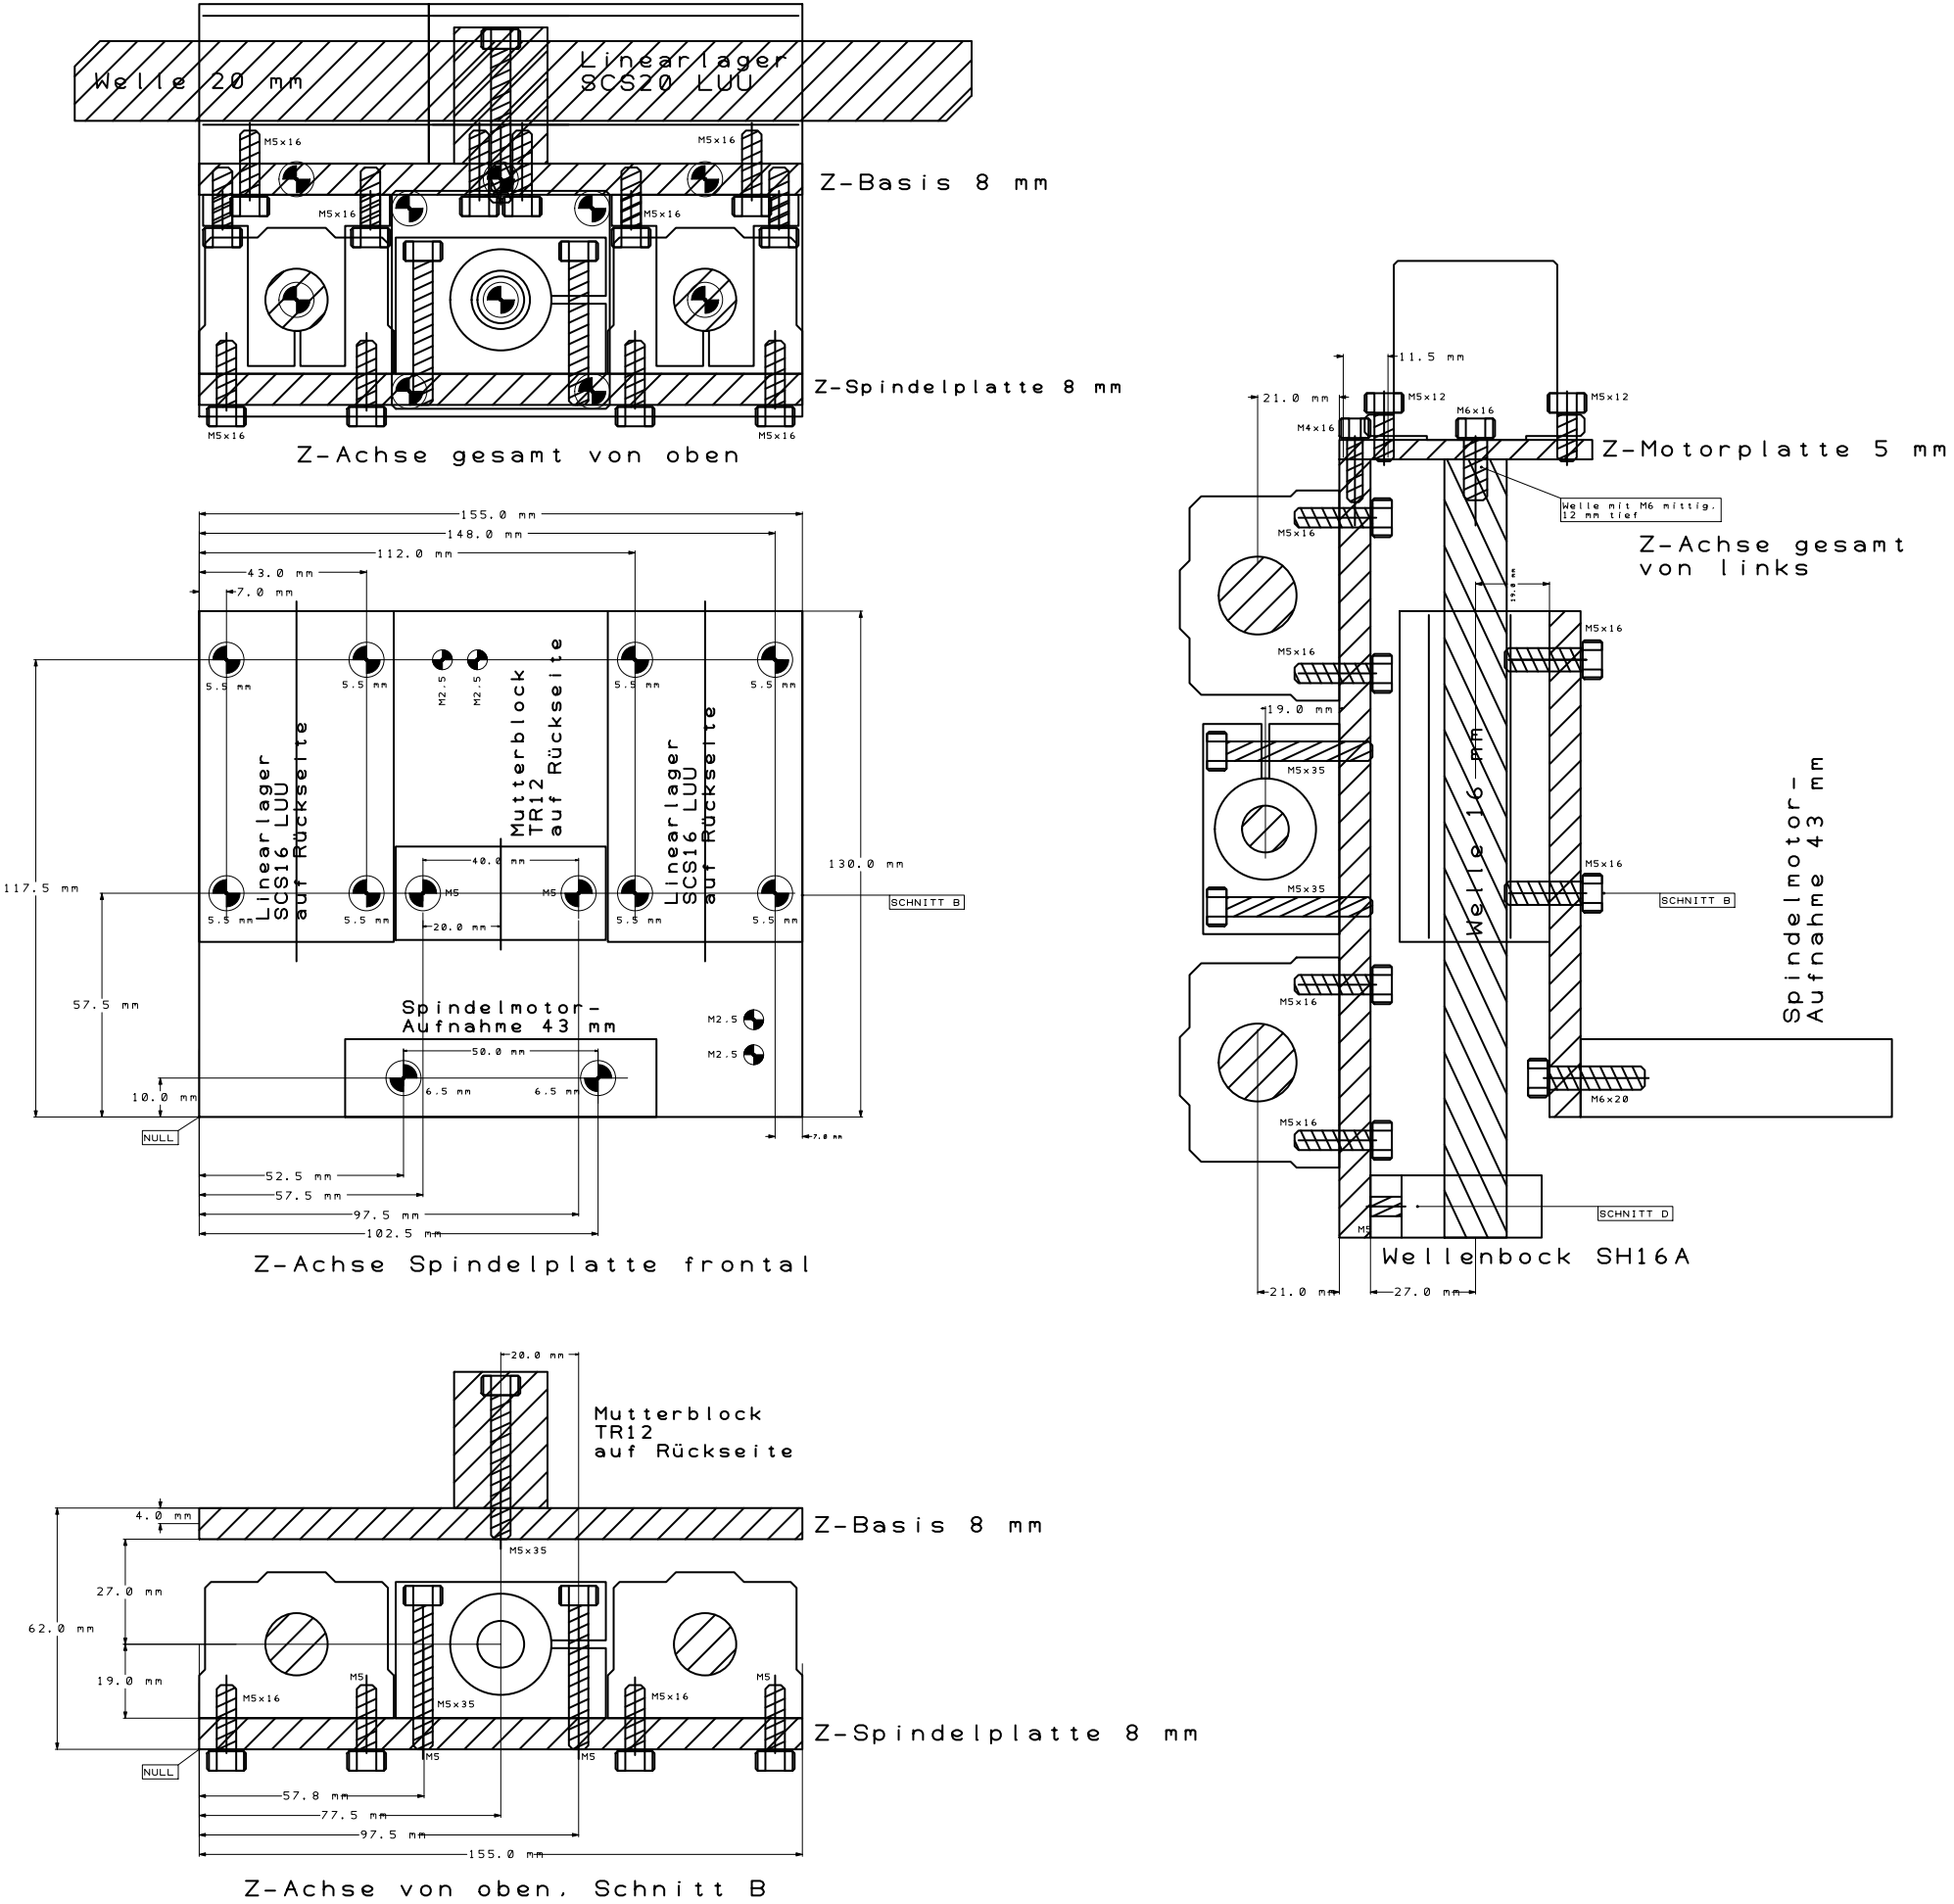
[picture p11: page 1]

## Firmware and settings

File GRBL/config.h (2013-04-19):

/*
  config.h - compile time configuration
  Part of Grbl

  Copyright (c) 2009-2011 Simen Svale Skogsrud
  Copyright (c) 2011-2012 Sungeun K. Jeon

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
   Some Q&D extensions by cm@ct.de for use with chinese stepper driver board.
   See settings.c and settings.h for more #defines!
*/

#ifndef config_h
#define config_h

// IMPORTANT: Any changes here requires a full re-compiling of the source code to propagate them.

#define BAUD_RATE 9600

// Define pin-assignments
#define STEPPING_DDR       DDRD
#define STEPPING_PORT      PORTD
#define X_STEP_BIT         2  // Uno Digital Pin 2
#define Y_STEP_BIT         3  // Uno Digital Pin 3
#define Z_STEP_BIT         4  // Uno Digital Pin 4
#define X_DIRECTION_BIT    5  // Uno Digital Pin 5
#define Y_DIRECTION_BIT    6  // Uno Digital Pin 6
#define Z_DIRECTION_BIT    7  // Uno Digital Pin 7

#define STEPPERS_ENABLE_DDR    DDRB
#define STEPPERS_ENABLE_PORT   PORTB
#define STEPPERS_ENABLE_BIT    0  // Uno Digital Pin 8
#define STEPPERS_ACTIVITY_BIT  5  // "active" red LED on MikroE MINI-AT board

#define LIMIT_DDR     DDRB
#define LIMIT_PIN     PINB
#define LIMIT_INVMASK 0x00 // $0E for mechaStep/WinPC-NC compatible HW, $00 for chinese stepper driver board
#define X_LIMIT_BIT   1    // Uno Digital Pin 9
#define Y_LIMIT_BIT   2    // Uno Digital Pin 10
#define Z_LIMIT_BIT   3    // Uno Digital Pin 11

#define X_LIMIT_PRESENT
#define Y_LIMIT_PRESENT
#define Z_LIMIT_PRESENT
#define Y_HOME_FIRST	// swap home run order, Y first

#define HOMING_CYCLE 80 // cycle time for homing, depends on pulses per step (here 80 for 1600 = 1/8 step mode)
#define HOMING_LEAVE_PULSES 100 // additional number of pulses after leaving limit switches
// #define HOMING_ON_RESET // enable homing on reset

#define SPINDLE_ENABLE_DDR DDRB
#define SPINDLE_ENABLE_PORT PORTB
#define SPINDLE_ENABLE_BIT 4  // Uno Digital Pin 12

// #define SPINDLE_DIRECTION_DDR DDRB
// #define SPINDLE_DIRECTION_PORT PORTB
// #define SPINDLE_DIRECTION_BIT 5  // Uno Digital Pin 13, auf Activity LED!

#define AUX_DDR 	DDRC
#define AUX_PORT	PORTC
#define AUX_PIN		PINC
#define AUX_DDRVAL 	0x19     // DDR init value, all 0s become inputs with pullups
#define AUX_COUNTER_RESET 0  // External counter reset, used with M100 command
#define AUX_16_BIT 1         // Tool length input AUX_16
#define AUX_17_BIT 2
#define AUX_WDOG_BIT 3       // Activity monitor square wave
#define AUX_SERVO_BIT 4
#define AUX_STOP_BIT 5
#define AUX_INVMASK 0x00     // $20 for mechaStep/WinPC-NC compatible HW, $00 for Mach3

// Switch Report on "%" character:
// Bit 0 = X Limit (+1)  X_LIMIT_BIT
// Bit 1 = Y Limit (+2)  Y_LIMIT_BIT
// Bit 2 = Z Limit (+4)  Z_LIMIT_BIT
// Bit 3 = Aux_16  (+8)  AUX_16_BIT
// Bit 4 = Aux_17  (+16) AUX_16_BIT
// Bit 5 = E-Stop  (+32) AUX_STOP_BIT
// e.g. %Sw:[33] = E-Stop and X-Limit

// Steigung der verwendeten Spindeln in mm pro Umdrehung
// nur zur Berechnung der Default-Einstellungen, siehe settings.c
#define THREAD_PITCH 3.0
// Motor-Pulse pro Umdrehung, 1600 für Achtelschritt-Betrieb
#define STEPS_PER_TURN 1600

// Define runtime command special characters. These characters are 'picked-off' directly from the
// serial read data stream and are not passed to the grbl line execution parser. Select characters
// that do not and must not exist in the streamed g-code program. ASCII control characters may be
// used, if they are available per user setup. Also, extended ASCII codes (>127), which are never in
// g-code programs, maybe selected for interface programs.
// TODO: Solidify these default characters. Temporary for now.
#define CMD_STATUS_REPORT '?'
#define CMD_SWITCH_REPORT '%'
#define CMD_FEED_HOLD '!'
#define CMD_CYCLE_START '~'
#define CMD_RESET 0x18 // ctrl-x

// Specifies the number of work coordinate systems grbl will support (G54 - G59).
// This parameter must be one or greater, currently supporting up to a value of 6.
#define N_COORDINATE_SYSTEM 1

// This parameter sets the delay time before disabling the steppers after the final block of movement.
// A short delay ensures the steppers come to a complete stop and the residual inertial force in the
// CNC axes don't cause the axes to drift off position. This is particularly important when manually
// entering g-code into grbl, i.e. locating part zero or simple manual machining. If the axes drift,
// grbl has no way to know this has happened, since stepper motors are open-loop control. Depending
// on the machine, this parameter may need to be larger or smaller than the default time.
// NOTE: If commented out, the delay will not be compiled.
#define STEPPER_IDLE_LOCK_TIME 25 // (milliseconds) - Integer > 0
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

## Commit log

2013-02-22 new files
    [mechanical_parts_list.xls]
2013-02-22 part list
    [mechanical_parts_list.xls]
2013-02-22 new LabVIEW files
    [MINIvice - Drill Data - Through Hole (Unplated).drl, MINIvice - Drill Data - Through Hole.drl, MTG2 - Drill Data - Through Hole (Unplated).drl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]
2013-04-19 Version 0.8a3/cm
    [config.h]
2013-04-19 Version 0.8a3/cm für Trapezspindeln mit 6mm Steigung
2013-04-19 Milling Software 1.1 for LabVIEW 6.1 and up
2013-04-19 mit alternativer Z-Achse
    [mechanical_parts_list.xls]
2013-05-06 reverse engin'd china stepper schematic

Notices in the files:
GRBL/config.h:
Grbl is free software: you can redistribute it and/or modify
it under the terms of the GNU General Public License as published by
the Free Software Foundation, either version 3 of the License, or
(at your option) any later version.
